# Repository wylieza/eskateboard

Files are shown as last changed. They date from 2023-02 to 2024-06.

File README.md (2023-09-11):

## Electric Skateboard Project

Contains all the collaborative project files for Justin and Stefans
electic skateboard project.

## Versioning
### Release Version: V0.7.0
Latest Releases
  - battery container	V0.1.0
  - battery cover	V0.2.1
  - mounting plate	V0.3.0
  - bms breakout	V1.0.0
  - battery breakout    V1.0.1
  - electronics mount V1.0.0

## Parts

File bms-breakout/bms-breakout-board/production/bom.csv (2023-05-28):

Designator | Footprint | Quantity | Value | LCSC Part #
J1, J2, J3, J4, J5, J6 | PinHeader_1x04_P2.00mm_Horizontal | 6 | Conn_01x04
J7 | PinHeader_1x11_P2.54mm_Vertical | 1 | Conn_01x11

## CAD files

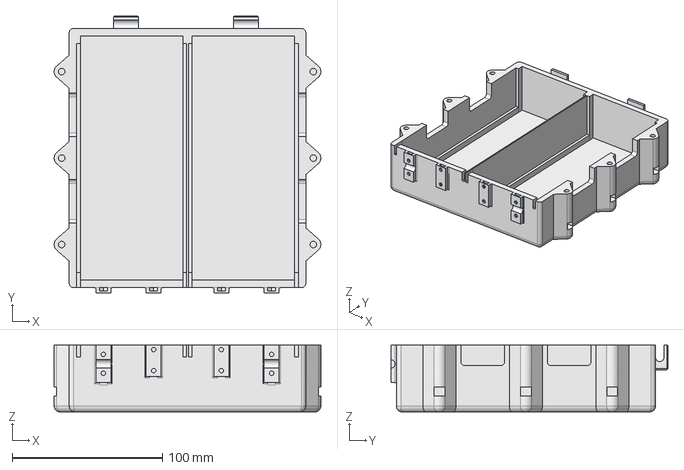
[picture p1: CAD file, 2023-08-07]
battery_pack/battery_box/eskate-battery.FCStd
177.4 x 184.2 x 44.5 mm

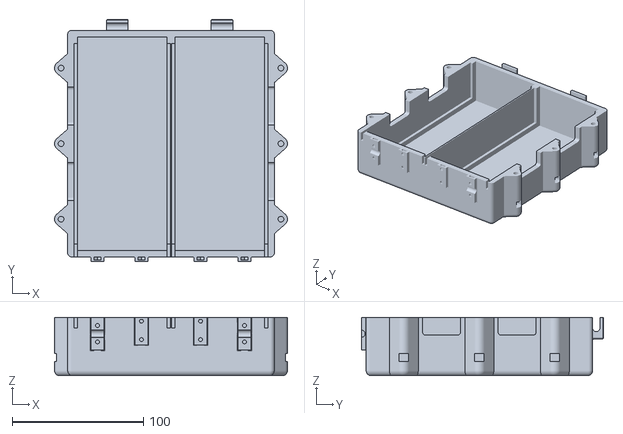
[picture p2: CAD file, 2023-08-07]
battery_pack/battery_box/exports/eskate-battery-container-V0.3.0.stl
177.4 x 184.2 x 44.5

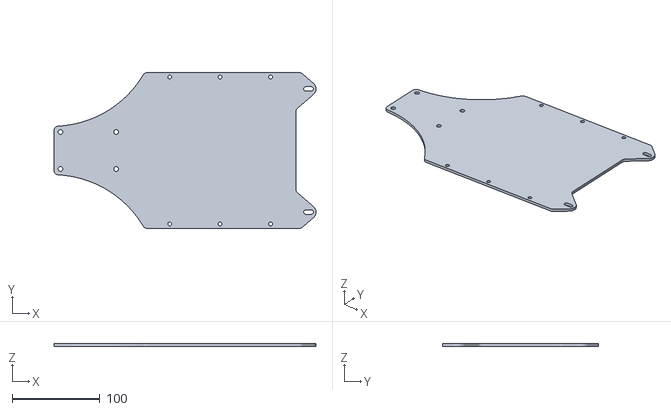
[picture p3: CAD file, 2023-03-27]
battery_pack/mounting_plate/exports/battery-plate-V0.3.0.stl
298.6 x 177.4 x 3.00

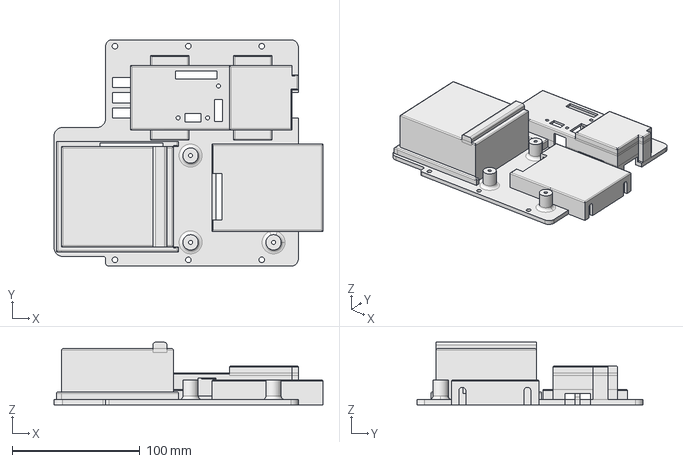
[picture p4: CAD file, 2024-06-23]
electronics_mount/electronics-mount.FCStd
210.7 x 177.4 x 49.0 mm

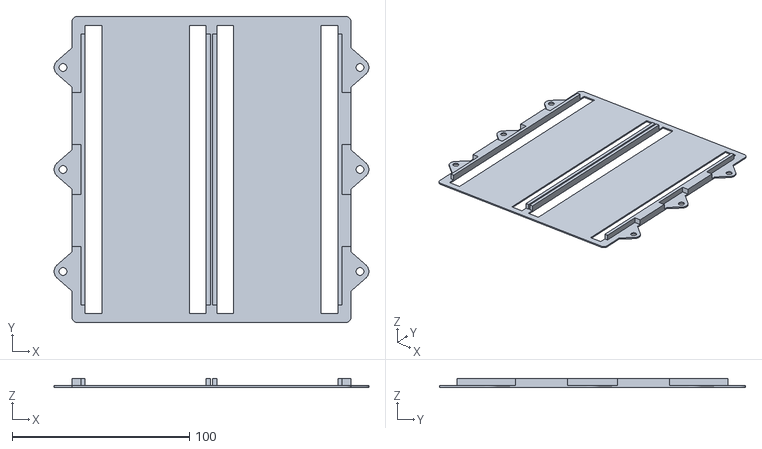
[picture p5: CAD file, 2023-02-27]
battery_pack/battery_box/exports/eskate-battery-cover-V0.2.1.stl
177.4 x 172.5 x 5.00

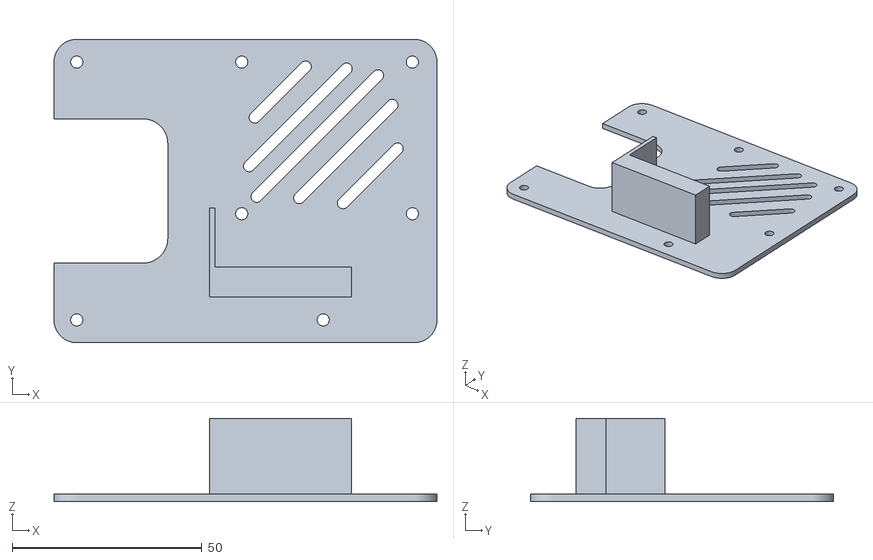
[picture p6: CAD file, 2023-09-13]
electronics_mount/exports/receiver-and-balance-breakout-V-0-2-0.stl
101.0 x 80.0 x 22.0

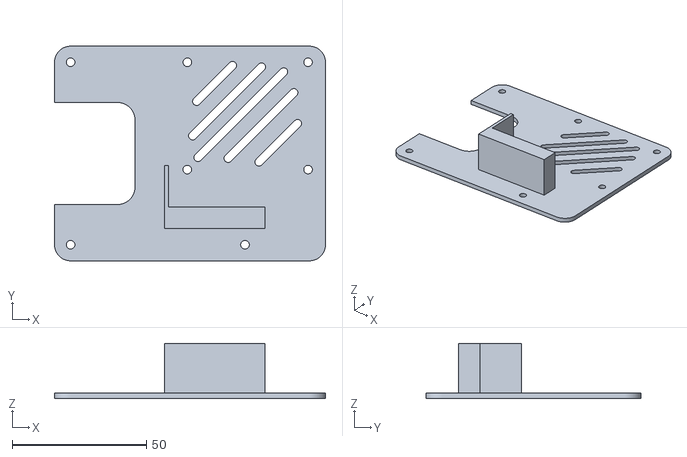
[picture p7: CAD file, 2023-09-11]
electronics_mount/exports/receiver-and-balance-breakout-V-0-1-0.stl
101.0 x 80.0 x 20.5

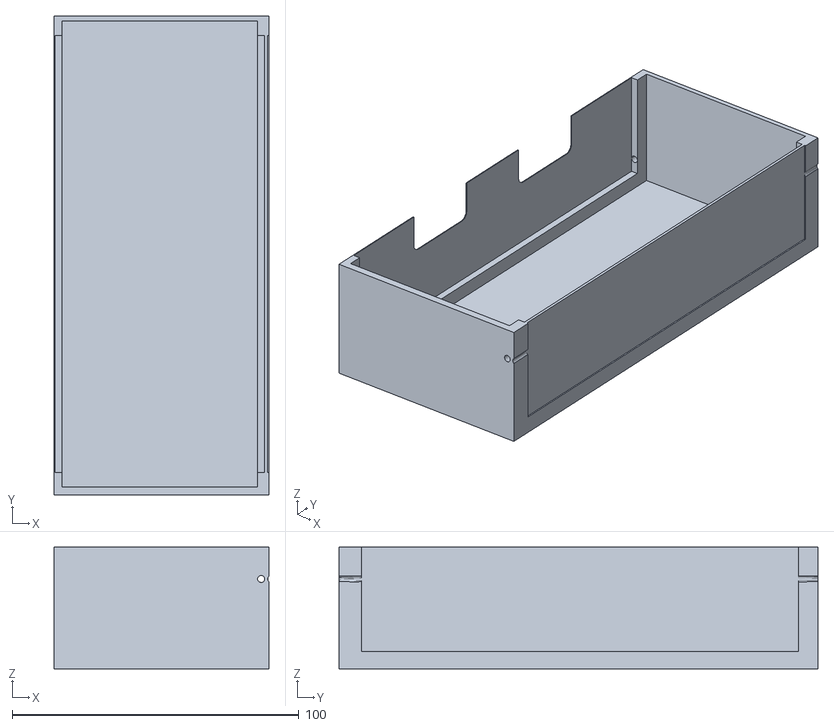
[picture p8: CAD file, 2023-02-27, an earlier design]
battery_pack/battery_box/print-archive/eskate-battery-container-V0.1.0-crop-1.stl
75.0 x 167.0 x 42.5

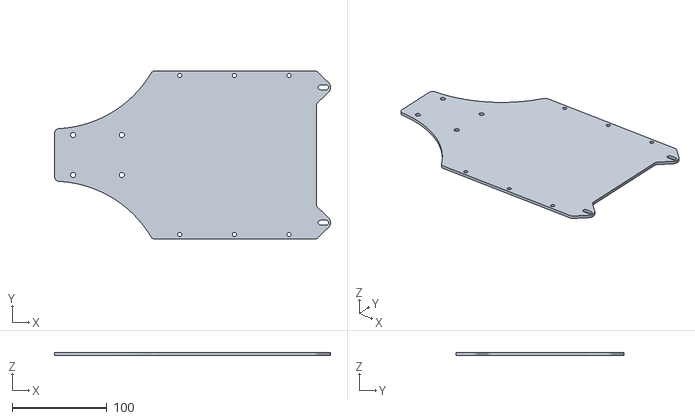
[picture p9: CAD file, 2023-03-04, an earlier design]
battery_pack/mounting_plate/exports/battery-plate-V0.2.0.stl
290.6 x 177.4 x 3.00

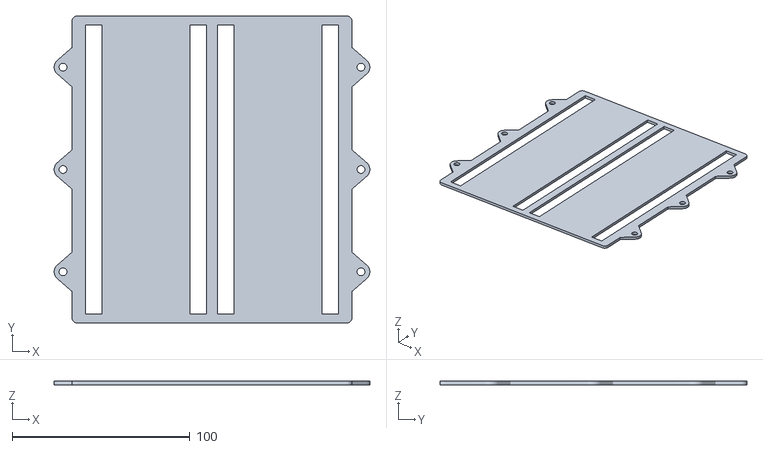
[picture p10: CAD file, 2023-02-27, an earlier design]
battery_pack/battery_box/exports/eskate-battery-cover-V0.1.0.stl
177.4 x 172.5 x 2.00

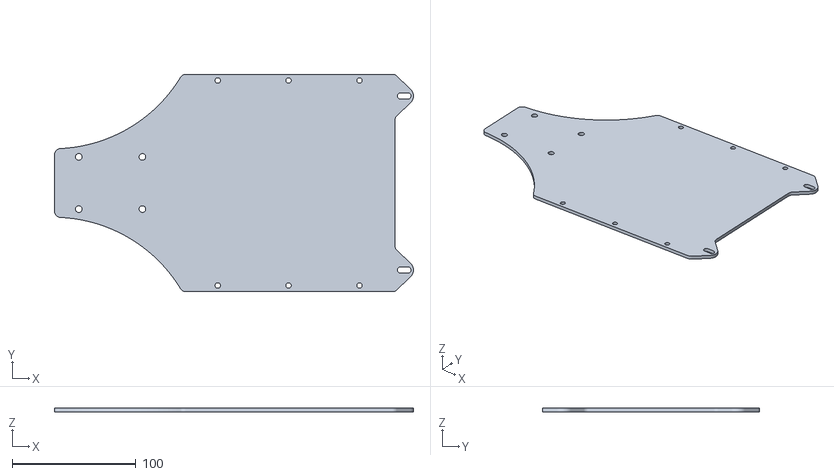
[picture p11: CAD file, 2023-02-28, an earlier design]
battery_pack/mounting_plate/exports/battery-plate-V0.1.0.stl
289.6 x 175.4 x 3.00

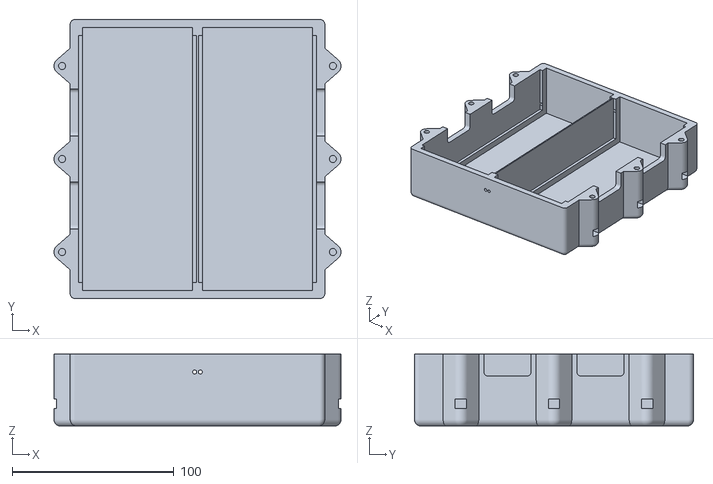
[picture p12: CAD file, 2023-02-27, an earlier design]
battery_pack/battery_box/exports/eskate-battery-container-V0.1.0.stl
177.4 x 172.5 x 44.5

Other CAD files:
battery_pack/mounting_plate/Plate.FCStd
electronics_mount/exports/electronics-mount-housing-V-1-1-0.stl
electronics_mount/receiver-and-balance-breakout.FCStd
electronics_mount/exports/electronics-mount-housing-V-1-0-0.stl
battery_pack/battery_box/exports/eskate-battery-cover-V0.2.0.stl

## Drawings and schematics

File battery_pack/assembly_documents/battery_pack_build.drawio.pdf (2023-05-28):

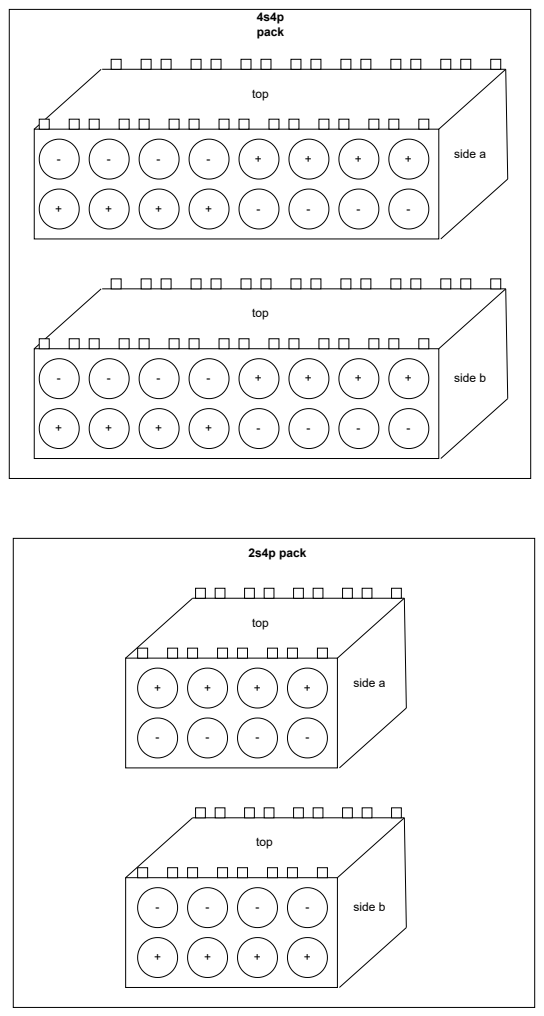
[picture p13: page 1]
top; side a; side b; 4s4p pack; 2s4p pack

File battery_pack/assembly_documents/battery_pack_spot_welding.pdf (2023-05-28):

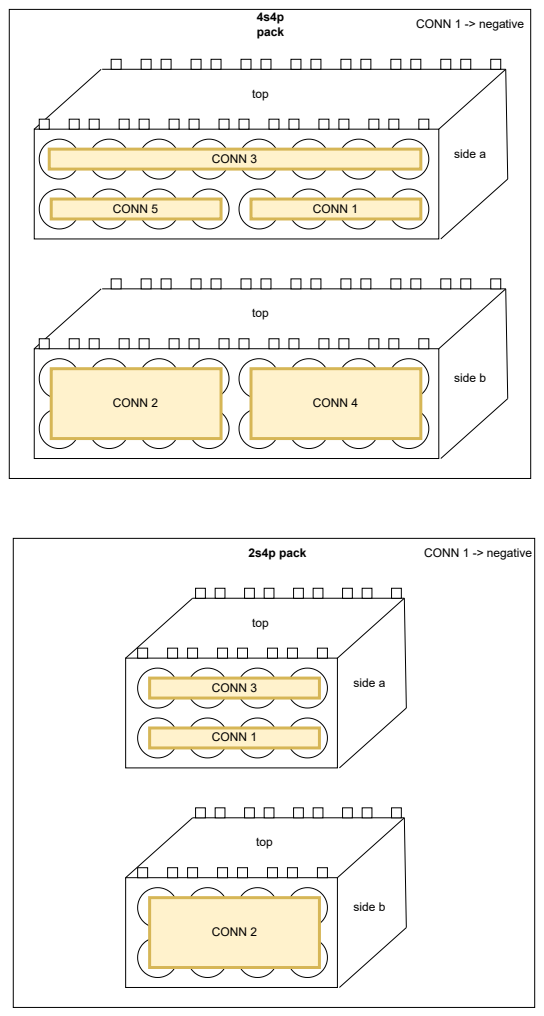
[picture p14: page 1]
CONN 5; CONN 1; CONN 3; CONN 2; CONN 4; top; side a; side b; 4s4p pack; 2s4p pack; CONN 1 -> negative

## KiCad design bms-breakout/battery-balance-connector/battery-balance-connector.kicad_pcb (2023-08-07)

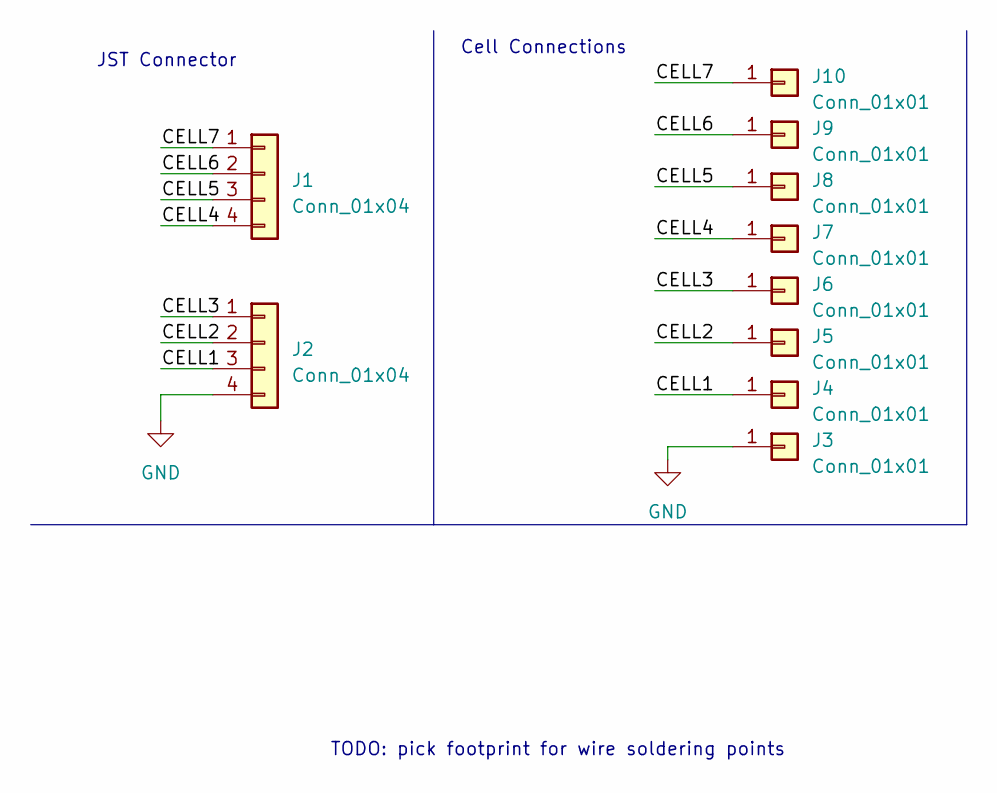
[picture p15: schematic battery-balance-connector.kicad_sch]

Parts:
J1, J2: Conn_01x04; JST_PH_B4B-PH-K_1x04_P2.00mm_Vertical
J3, J4, J5, J6, J7, J8, J9, J10: Conn_01x01; SolderWirePad_1x01_SMD_2x4mm_2.7mmRelief

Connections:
/CELL1: J2.3, J4.1
/CELL2: J2.2, J5.1
/CELL3: J2.1, J6.1
/CELL4: J1.4, J7.1
/CELL5: J1.3, J8.1
/CELL6: J1.2, J9.1
/CELL7: J1.1, J10.1
GND: J2.4, J3.1

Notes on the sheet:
TODO: pick footprint for wire soldering points
Cell Connections
JST Connector

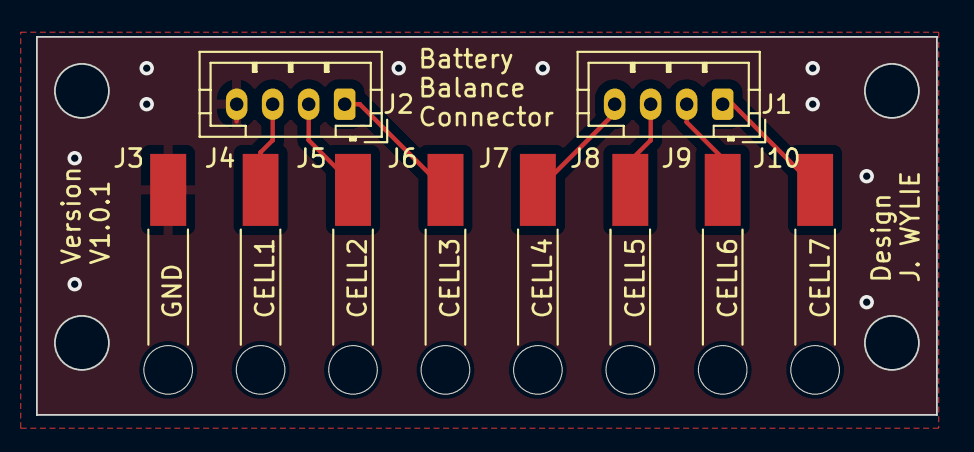
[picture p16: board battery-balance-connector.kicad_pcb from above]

Board: 2 copper layers, 50.0 x 21.0 mm, 10 parts (0 on the bottom side), 8 nets.

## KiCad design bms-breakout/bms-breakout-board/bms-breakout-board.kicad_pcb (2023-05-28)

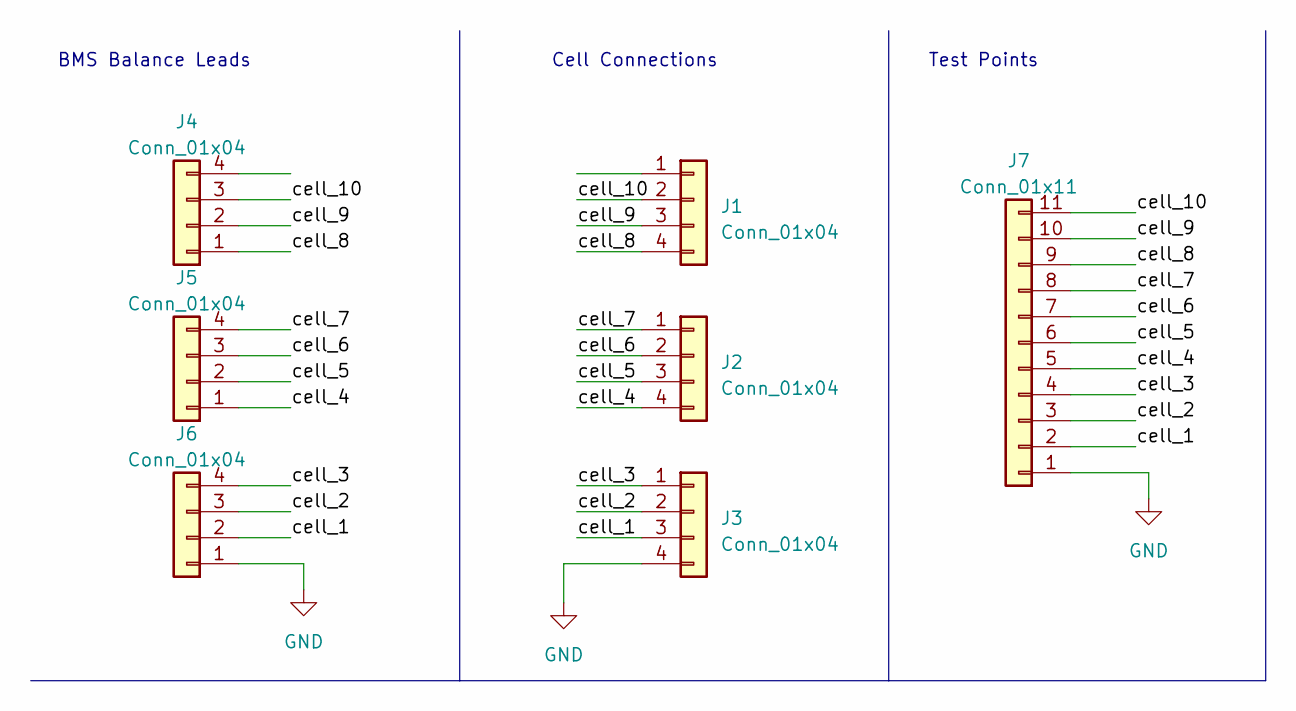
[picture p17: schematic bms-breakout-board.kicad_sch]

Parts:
J1, J2, J3, J4, J5, J6: Conn_01x04; PinHeader_1x04_P2.00mm_Horizontal
J7: Conn_01x11; PinHeader_1x11_P2.54mm_Vertical

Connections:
/cell_1: J3.3, J6.2, J7.2
/cell_2: J3.2, J6.3, J7.3
/cell_3: J3.1, J6.4, J7.4
/cell_4: J2.4, J5.1, J7.5
/cell_5: J2.3, J5.2, J7.6
/cell_6: J2.2, J5.3, J7.7
/cell_7: J2.1, J5.4, J7.8
/cell_8: J1.4, J4.1, J7.9
/cell_9: J1.3, J4.2, J7.10
/cell_10: J1.2, J4.3, J7.11
GND: J3.4, J6.1, J7.1

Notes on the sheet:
Test Points
Cell Connections
BMS Balance Leads

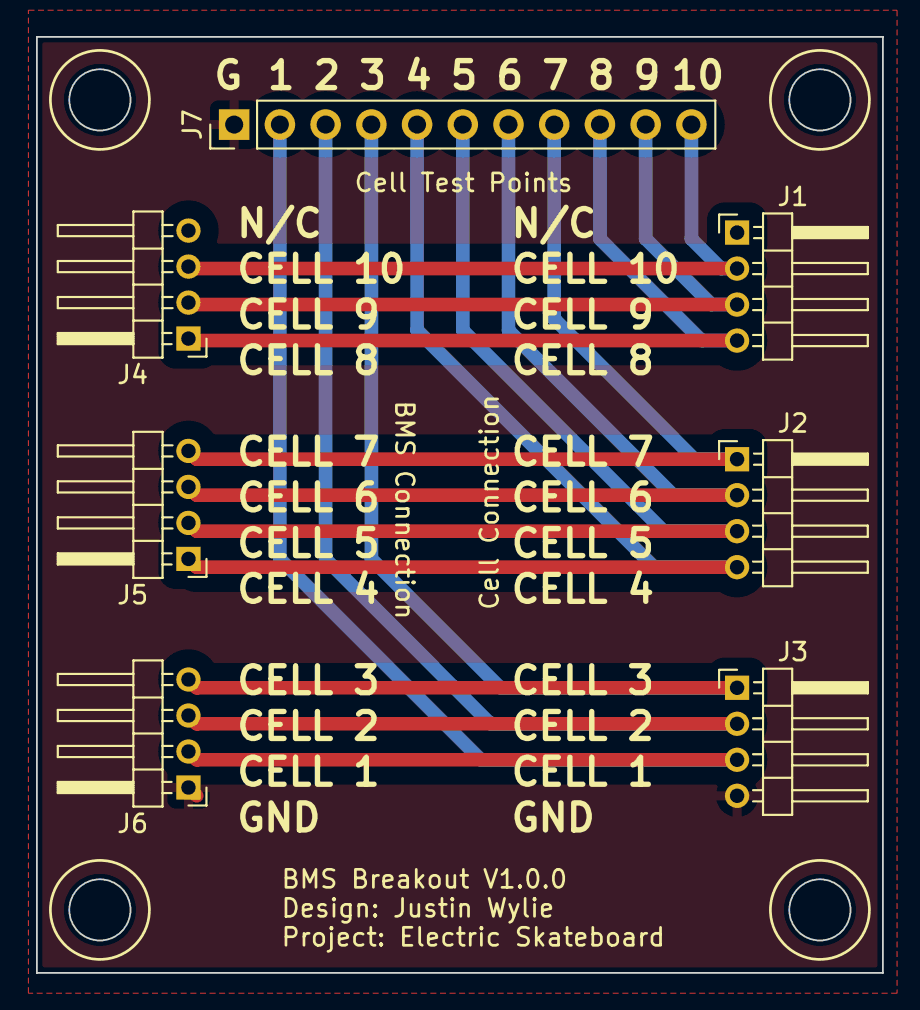
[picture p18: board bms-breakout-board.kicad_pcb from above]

Board: 2 copper layers, 47.0 x 52.0 mm, 7 parts (0 on the bottom side), 11 nets.

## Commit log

2022-10-23 added my sketch to the repo
    [Plate.FCStd]
2022-10-24 finished piece, needing to still update mounting holes
    [Plate.FCStd]
2022-10-25 adding work so far to repo
    [eskate-battery.FCStd]
2022-10-26 side mounting holes for box
    [eskate-battery.FCStd]
2022-10-26 box taking shape - just need to add nuts and probably a bit of tweaking
    [eskate-battery.FCStd]
2022-10-27 added nut insets and slots for mounting
    [eskate-battery.FCStd]
2022-10-27 moved bolt holes so they don't go through entire shape
    [eskate-battery.FCStd]
2022-10-27 chamfer edges
    [eskate-battery.FCStd]
2022-10-29 using m4 nuts and bolts for mounting to plate. Added balance lead holes
    [eskate-battery.FCStd]
2022-10-29 export to stl
    [eskate-battery-container.stl]
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2022-10-31 updated battery mounting hole location
    [Plate.FCStd]
2022-11-01 turned mounting hole into slot
    [Plate.FCStd]
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2022-11-14 added tolerance to width, but not length yet because sketch breaks
    [eskate-battery.FCStd]
2022-11-19 added 0.6mm tollerance to width and length of battery
    [eskate-battery-container.stl, eskate-battery.FCStd]
2022-11-21 increasing tolerance futher
    [eskate-battery-container.stl, eskate-battery.FCStd]
2023-02-21 now using versioning to keep track of things
    [eskate-battery-container-V0.1.0.stl, eskate-battery-container.stl, eskate-battery.FCStd]
2023-02-26 cropped print to test fit for V0.1.0
    [eskate-battery-container-V0.1.0-crop-1.stl]
2023-02-26 created a cover for the battery box
    [eskate-battery-cover-V0.1.0.stl, eskate-battery.FCStd]
2023-02-27 added keying and made the box cover much thiner - V0.2.0
    [eskate-battery-cover-V0.2.0.stl, eskate-battery.FCStd]
2023-02-27 fixed non-manifold issue with box cover - V0.2.1
    [eskate-battery-cover-V0.2.1.stl, eskate-battery.FCStd]
2023-02-28 version number for plate and stl export
    [Plate.FCStd, battery-plate-V0.1.0.stl]
2023-02-28 updated for tolerances
    [Plate.FCStd]
2023-03-04 battery plate updated to V0.2.0
    [Plate.FCStd, battery-plate-V0.2.0.stl]
2023-03-15 added gap for mounting holes
    [Plate.FCStd]
2023-03-16 remeasured the distance between truck holes
    [Plate.FCStd]
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2023-05-26 begin work on the electronics mounting
    [Plate.FCStd, electronics-mount.FCStd]
2023-05-26 taking form in 3D - much tweaking ahead (and plenty more design)
    [electronics-mount.FCStd]
2023-05-27 started work on the bms breakout
    [bms-breakout-board.kicad_pcb, bms-breakout-board.kicad_sch, bom.csv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]
2023-05-27 cell balancing breakout board layout pretty much done
    [bms-breakout-board.kicad_pcb]
2023-05-28 finished v1.0.0 of bms breakout
    [bms-breakout-board-B_Cu.gbl, bms-breakout-board-B_Mask.gbs, bms-breakout-board-B_Paste.gbp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]
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2023-06-03 much work on the esc component of electrics mounting
    [electronics-mount.FCStd]
2023-06-04 esc adjusted tollerances for better fit. much work on port access
    [electronics-mount.FCStd]
2023-06-04 working on the receiver cable stow away
    [electronics-mount.FCStd]
2023-06-05 added stow space for unused receiver cable
    [electronics-mount.FCStd]
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2023-06-08 not sure - no work done here
    [electronics-mount.FCStd]
2023-06-08 adding cable supports for securing cable to battery box
    [eskate-battery.FCStd]
2023-06-12 removed balance lead holes and fixed number of issues after I did that.... next I'll create slots for these leads
    [eskate-battery.FCStd]
2023-06-21 not sure here, but files changes
    [eskate-battery.FCStd]
2023-06-21 begin work on the front battery balance leads adapter board
    [battery-balance-connector.kicad_pcb, battery-balance-connector.kicad_sch]
2023-06-22 made some more progress on the battery balance connector
    [battery-balance-connector.kicad_pcb, battery-balance-connector.kicad_sch]
2023-06-24 V1.0.0 of battery balance connector
    [battery-balance-connector.kicad_pcb, battery-balance-connector.kicad_sch]
2023-06-24 V1.0.1 - using vertical mounting and tweaked dimensions
    [battery-balance-connector.kicad_pcb, battery-balance-connector.kicad_sch]
2023-06-24 gerbers for V1.0.1 of battery balance leads connector
    [battery-balance-connector.kicad_pcb]
2023-06-26 fixing up issue with some face error
    [eskate-battery.FCStd]
2023-06-26 work on the pcb mounting and added slots for balance leads on main container
    [eskate-battery.FCStd]
2023-07-03 finished cable support. added fillets. exported V0.3.0 stl for printing
    [eskate-battery-cover-V0.3.0.stl, eskate-battery.FCStd]
2023-07-04 renamed to correctly identify object - not cover, but container
    [eskate-battery-container-V0.3.0.stl]
2023-08-07 work on the battery and the bms cable slots and fit
    [electronics-mount.FCStd]
2023-08-09 final alignment of leads for bms before test print
    [electronics-mount.FCStd]
2023-08-12 added a mm length and width for bms fit
    [electronics-mount.FCStd]
2023-08-24 work on the positioning
    [electronics-mount.FCStd]
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2023-08-26 positioning bms and battery
    [electronics-mount.FCStd]
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2023-08-26 trying to figure out broken battery mount
    [electronics-mount.FCStd]
2023-08-26 calling it for now! will fix this battery issue later
    [electronics-mount.FCStd]
2023-09-02 finally figured out the issue with that battery section! flipping from bottom to top view was confusing me
    [electronics-mount.FCStd]
2023-09-03 accounting for balance lead going over top of battery
    [electronics-mount.FCStd]
2023-09-03 added mounting pillars - checkpoint before smoothing edges etc.
    [electronics-mount.FCStd]
2023-09-03 adding tons of fillets
    [electronics-mount.FCStd]
2023-09-11 releasing V0.7.0 with completed electronics mount
    [electronics-mount-housing-V-1-0-0.stl]
2023-09-11 created V0.1.0 of the receiver and balance lead breakout mount
    [receiver-and-balance-breakout-V-0-1-0.stl, receiver-and-balance-breakout.FCStd]
2023-09-13 corrected height of receiver encasing
    [receiver-and-balance-breakout-V-0-2-0.stl, receiver-and-balance-breakout.FCStd]
2024-06-23 improved supporot for battery on electronics mount for board
    [electronics-mount-housing-V-1-1-0.stl, electronics-mount.FCStd]
